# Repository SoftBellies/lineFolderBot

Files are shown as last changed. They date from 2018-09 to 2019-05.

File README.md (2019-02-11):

# Line Follower robot kit

le projet est de réaliser une soirée "initiation à l'électronique" dans le cadre d'un doctorat sauvage en numérique.

Les participants auront à construire un robot suiveur de ligne à partir d'un kit mis au point par le hackerspace.

Le présent dépot sert à la conception du kit et la rédaction de sa [notice](notice_fr.md)

# petit cahier des charges du kit

* Réalisable en moins de 4 heures en comptant le temps pour les indications, la formation des groupes, les tests.
* On initie à des techniques que les participants pourront réutiliser à la maison. Donc hormis un pistolet à colle, un fer à souder et un tourne-vis, aucun autre outil ne doit être à utiliser.
* Le robot peut être amélioré

C'est pour respecter ces trois points que je pars sur les concepts suivants:

* Le circuit électronique lors de l'atelier sera réalisé sur une plaque à pastille. Pas de création de circuits préimprimés à l'avance.
* L'utilisation d'un arduino permet de laisser une marge d'amélioration au robot (par l'ajout de capteurs ou de moteurs)

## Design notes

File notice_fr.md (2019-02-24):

# Notice de montage du robot suiveur de ligne

| Element | Quantité / notes | Image |
| :--- | :---: | ---: |
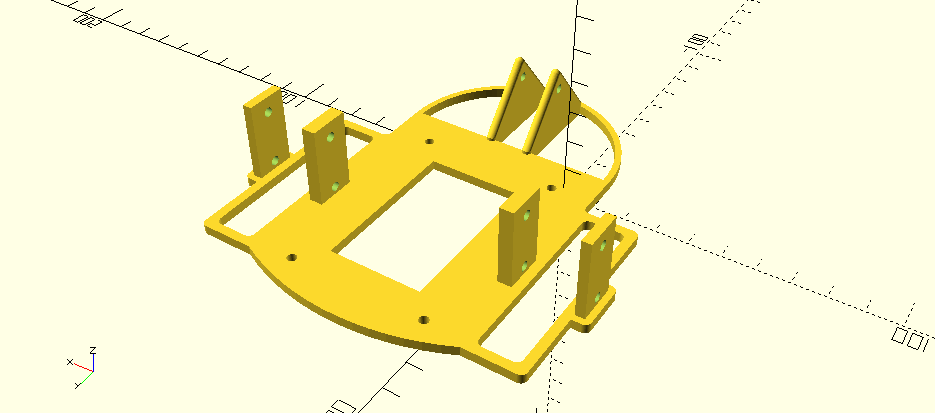
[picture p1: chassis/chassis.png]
chassis
| Chassis (impression 3D) | 1 | |
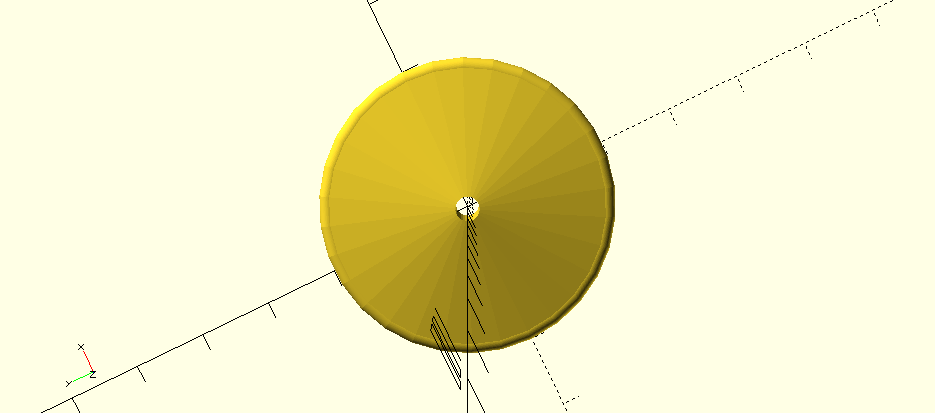
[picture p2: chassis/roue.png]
roue
|Roue arrière (impression 3D)|1||
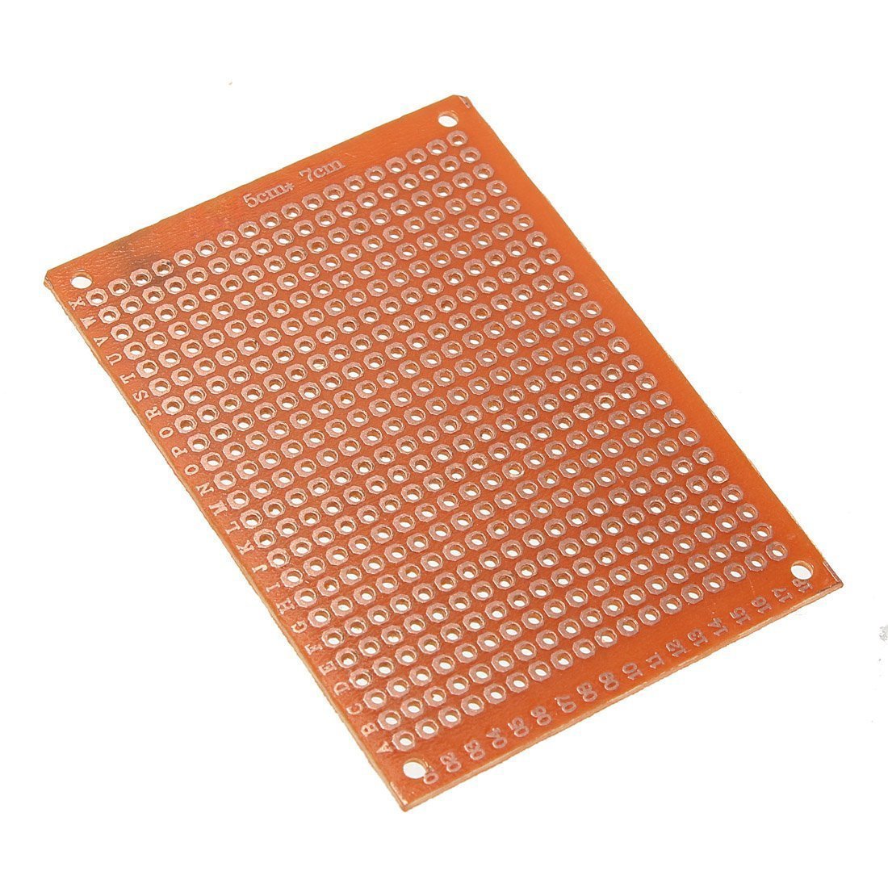
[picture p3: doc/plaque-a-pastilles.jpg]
|Plaque de prototypage à pastilles 5X7 CM|1|
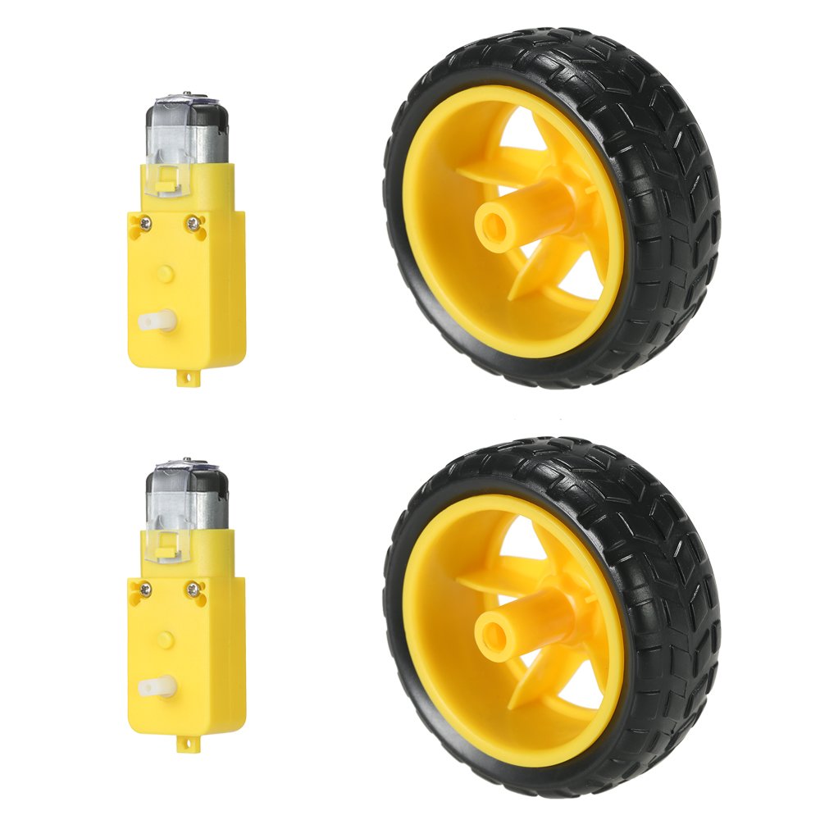
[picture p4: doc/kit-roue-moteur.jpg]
Kit roues et moteur
|kit Roues + moteur 5VDC|2|
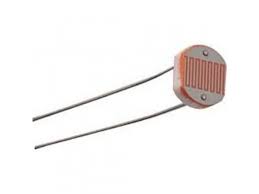
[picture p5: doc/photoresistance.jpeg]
photoresistance
|Photo résistances| 2 | |
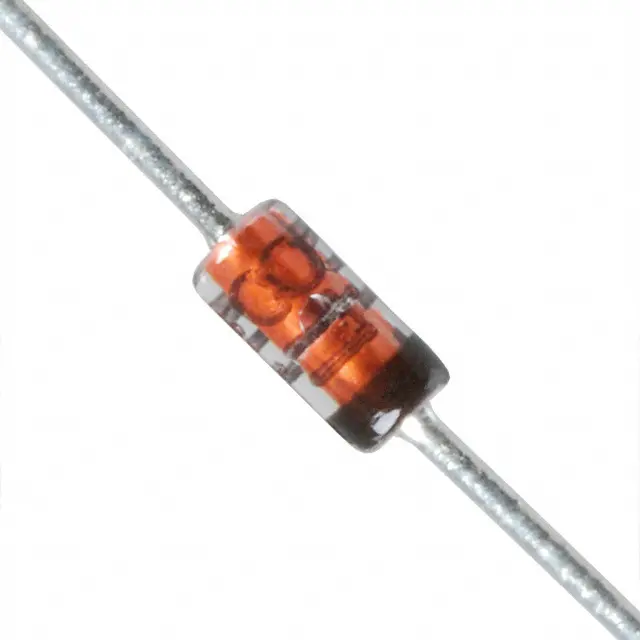
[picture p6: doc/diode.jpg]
diodes
|Diodes| 2 | |
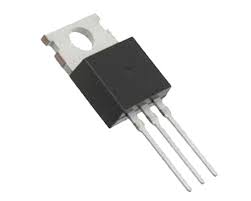
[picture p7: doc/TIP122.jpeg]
TIP122
|Transistor TIP 122| 2 | |
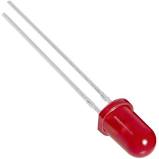
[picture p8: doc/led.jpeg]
leds
|Leds| 4 | |
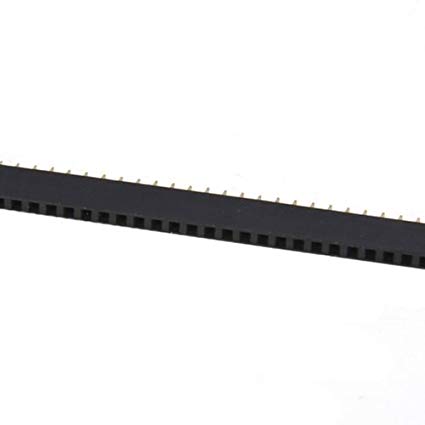
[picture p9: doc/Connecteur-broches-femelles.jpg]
connecteurs broches femelle
|Ligne connecteur broche femelle| 2x 15 + 2x2 ||

## Circuit électronique

Voici le shéma global :

Shema

La première face correspond aux pistes à créer sur la plaque à pastilles.

La seconde face est le côté composants.

### Les connecteurs femelles qui recevront l'arduino

* Prendre 2 rangées de connecteurs Pin femelles.
* Avec une pince coupante, les couper au milieu de la 16ème PIN, de façon à ce que 15 pins soient utilisables.

* Les placer sur la plaque de prototypage.

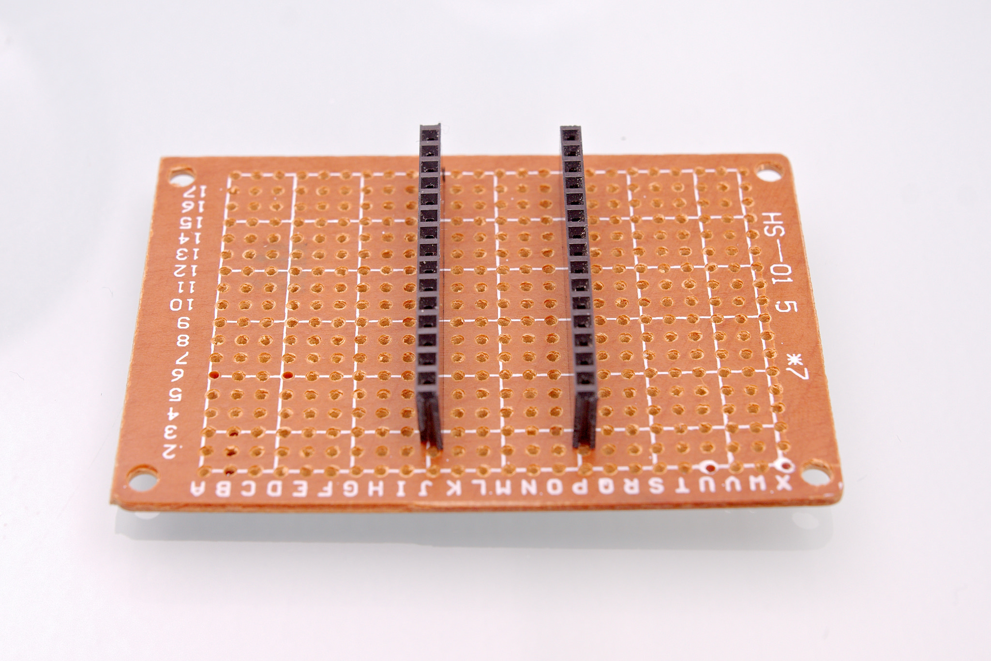
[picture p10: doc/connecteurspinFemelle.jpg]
photo connecteurs pins femelle


* Côté circuit, souder chaque pin:

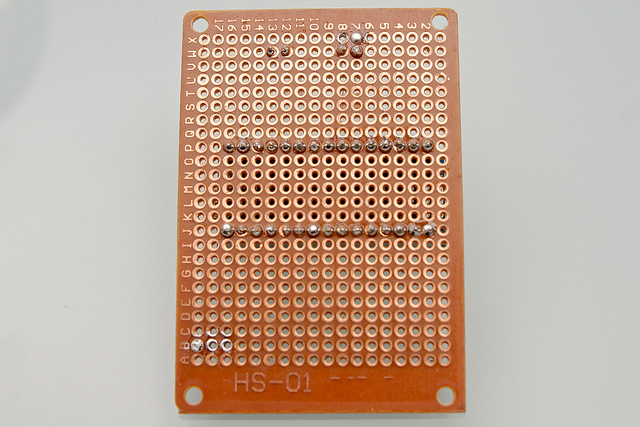
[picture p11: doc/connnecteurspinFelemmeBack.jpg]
photo connecteurs pins femelle verso


### La piste de masse

Afin de vous faire la main avec les soudures, Faites tout le circuit 5V (en rouge):

* En faisant en sorte que la continuité soit respectée.
* Sans déborder sur les pastilles d'à côté.

5V

### Souder quelques composants

* Coté composants de la plaque, placer ces trois résistances:

resistances

* Coté circuit, mettre un point de soudure sur les pattes des résistances pour les fixer (points marqués en rouge).

resistances

* Raccorder ces résistances à la masse de l'arduino:

resistances

Raccorder deux de ces résistances aux pins de l'arduino:

resistances

### Continuez !

Voila, vous avez compris, il faut placer les composants un par un, les souder et faire les lignes d'étain pour les relier conformément au circuit.

Le pas à pas s'arrête ici car c'est fastidieux à écrire. Continuez composant par composant, goutte d'étain par goutte d'étain.

Quelques subtilités cependant pour la suite:

#### Certains composants sont polarisés:

* Les LEDs; Sur le schéma, elles sont représentées vue de dessus. Le côté ayant un plat y est représenté. Disposez la LED sur votre circuit dans le même sens que sur le schéma.
* Les diodes; Un anneau noir est dessiné sur les diodes. Disposez-les en respectant le côté de l'anneau.
* Les transistors

#### le capteur doit froler le sol
Les LEDS et les photoresistances du capteur de ligne doivent être soudées de façon:
* la photoresistance doit être le plus près possible du sol
* La led ne doit pas éclairer directement la photoresistance, ses pattes doivent être plus courtes.

Comme ceci:

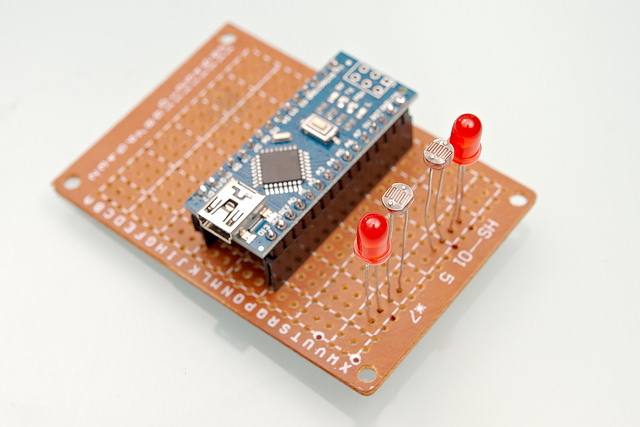
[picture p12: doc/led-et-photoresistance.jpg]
led


#### Composants sur l'autre face

Les Leds de Debugage doivent être côté circuit de la plaque, et non du même côté que les autres composants, afin qu'à la fin elles se retouvent au dessus du circuit.

## Arduino

Il faut souder les broches de l'arduino:

Le port USB doit être sur la face opposée aux broches.

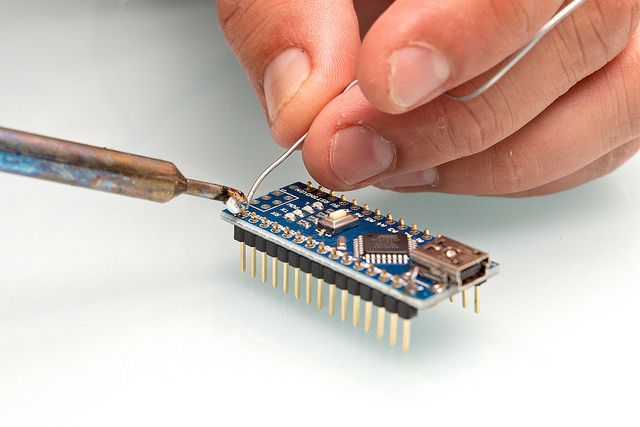
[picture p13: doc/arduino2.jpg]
arduino


## Fils  avec connecteurs Dupont sur les moteurs

Coupez un cable avec connecteurs Dupont male, dénudez-le et soudez-le sur les connecteurs du moteur. Comme ceci:

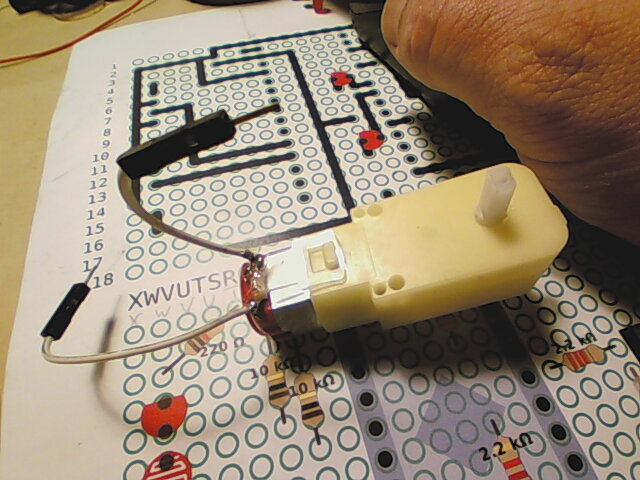
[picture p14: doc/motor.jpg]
motor


Longueur du fil, avec le connecteur: env. 7cm

## Tout assembler

Si nécessaire, contre-percez les trous dans le châssis et la plaque de prototypage.

Quelques coups de tourne-vis et vous aurez votre robot.

Il faut faire en sorte que les capteurs soient très près du sol.

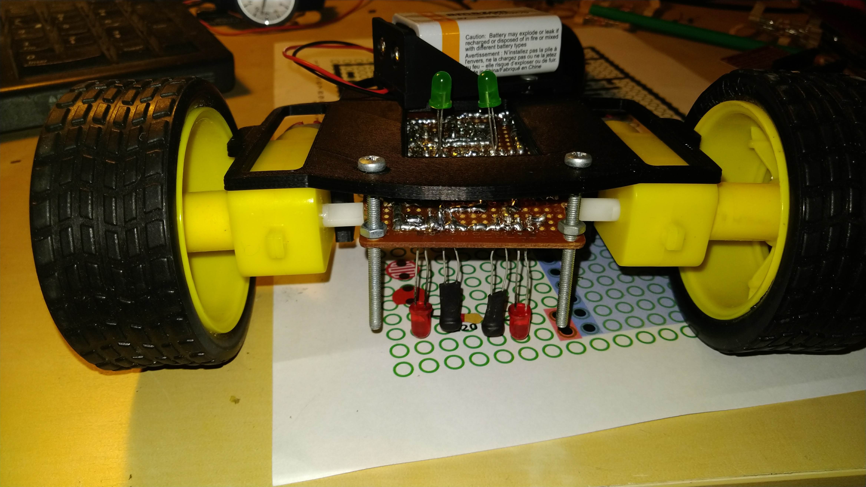
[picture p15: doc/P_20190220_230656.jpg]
robot


## Injecter le code dans l'arduino.

Il faut programmer l'arduino.

L'installation de l'environnement Arduino est expliquée sur le site officiel. https://www.arduino.cc/

Le programme servant à faire fonctionner le robot suiveur de ligne  peut être téléchargée sur la plateforme Gogs (git) du hackerspace:

https://git.ventresmous.fr/VentresMous/lineFollowerBot/src/master/lineFollowerBot/lineFollowerBot.ino

Nous vous détaillerons ces manipulations durant l'atelier.

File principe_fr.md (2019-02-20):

## Principes

### Détection de la ligne

Un sol clair reflète plus la lumière qu'un sol sombre.

En disposant de cette manière, deux LED et deux photoristances:

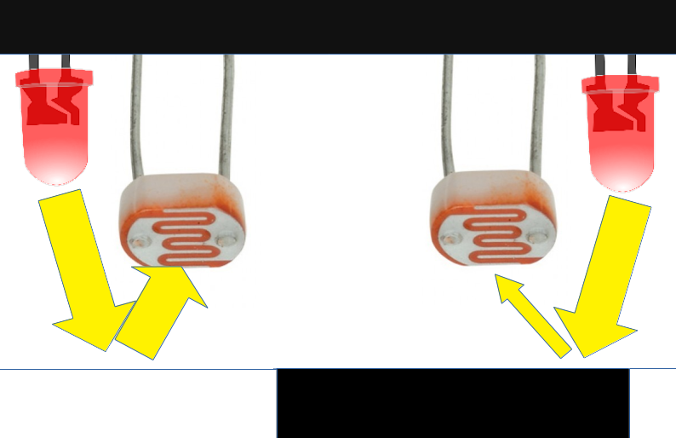
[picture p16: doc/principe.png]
schema de principe


La valeur de chaque photoresistance dépend de la quantité de lumière reflétée par le sol.

Sur le schéma ci dessus la lecture des valeurs des photorésistances permettrait de déduire que celle de droite est au dessus d'une ligne noire. Tandis que celle de gauche est au dessus d'une zone claire.

Le robot dérive donc vers la droite de la ligne. Il faut le faire tourner à gauche

### Actionner les moteurs en fonction des valeurs du capteur.

#### Présentation de l'arduino

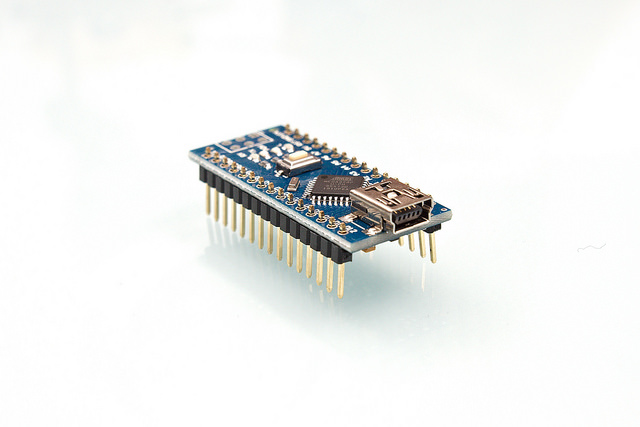
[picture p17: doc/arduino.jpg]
Arduino Nano


L'arduino est un circuit électronique programmable pouvant "lire des valeurs" via certaines pins, et déclencher des courants électriques via d'autres pins.

Grâce à cette carte pouvoir "lire" les valeurs des capteurs de luminosité, et notre programme, en fonction de ces valeurs actionnera ou non l'envoi d'une tension électrique dans les moteurs.

#### Lecture d'une valeur

#### déclenchement d'un moteur

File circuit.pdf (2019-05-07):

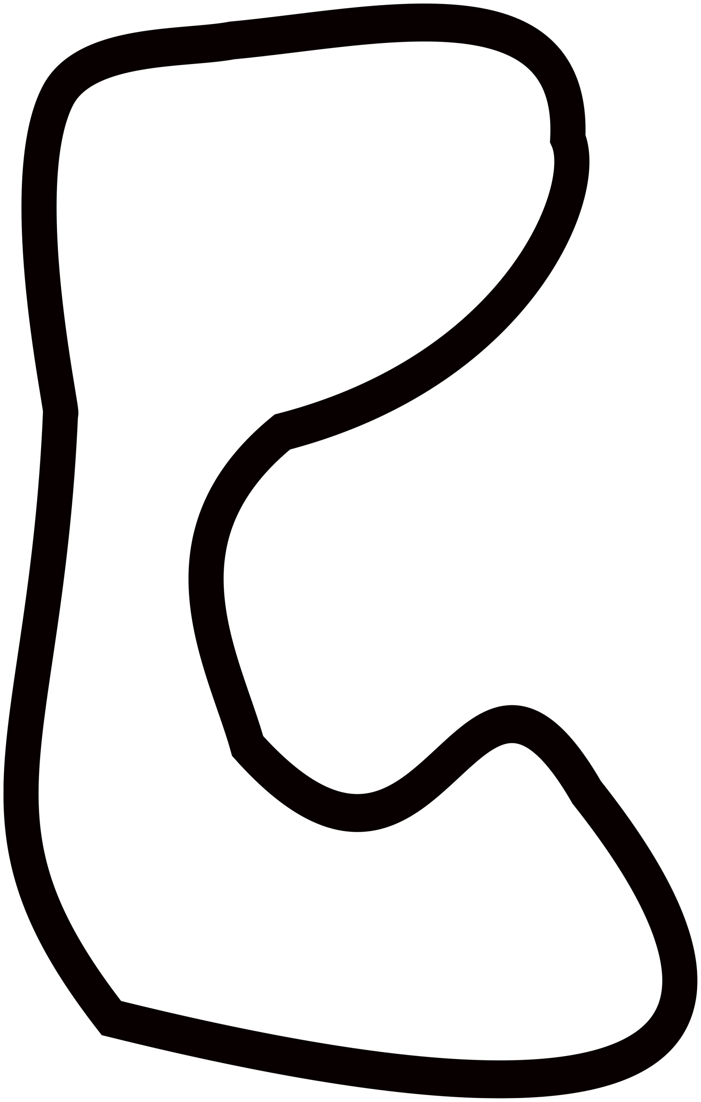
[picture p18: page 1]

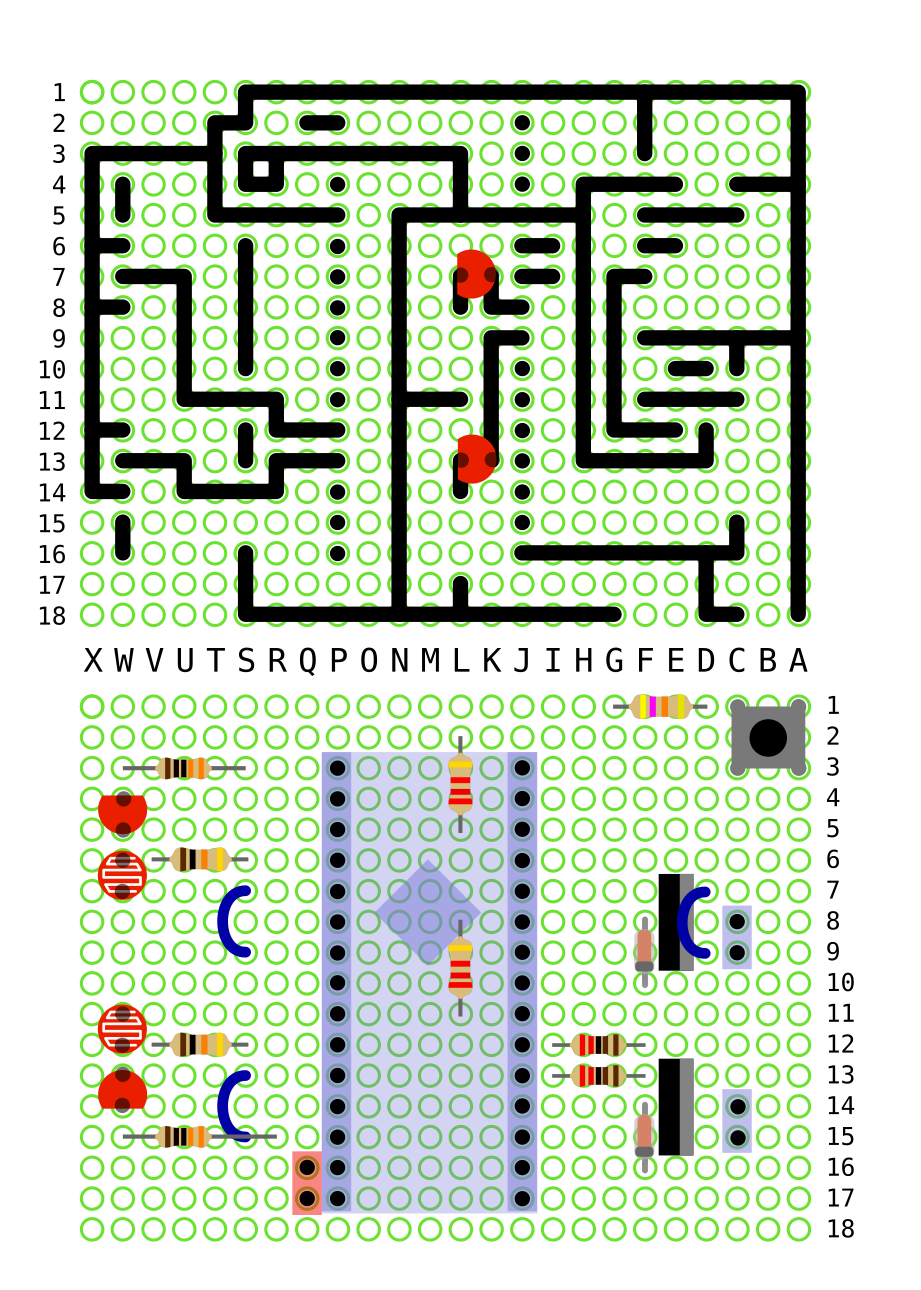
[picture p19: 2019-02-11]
electronics/robot-soudure-composants.png

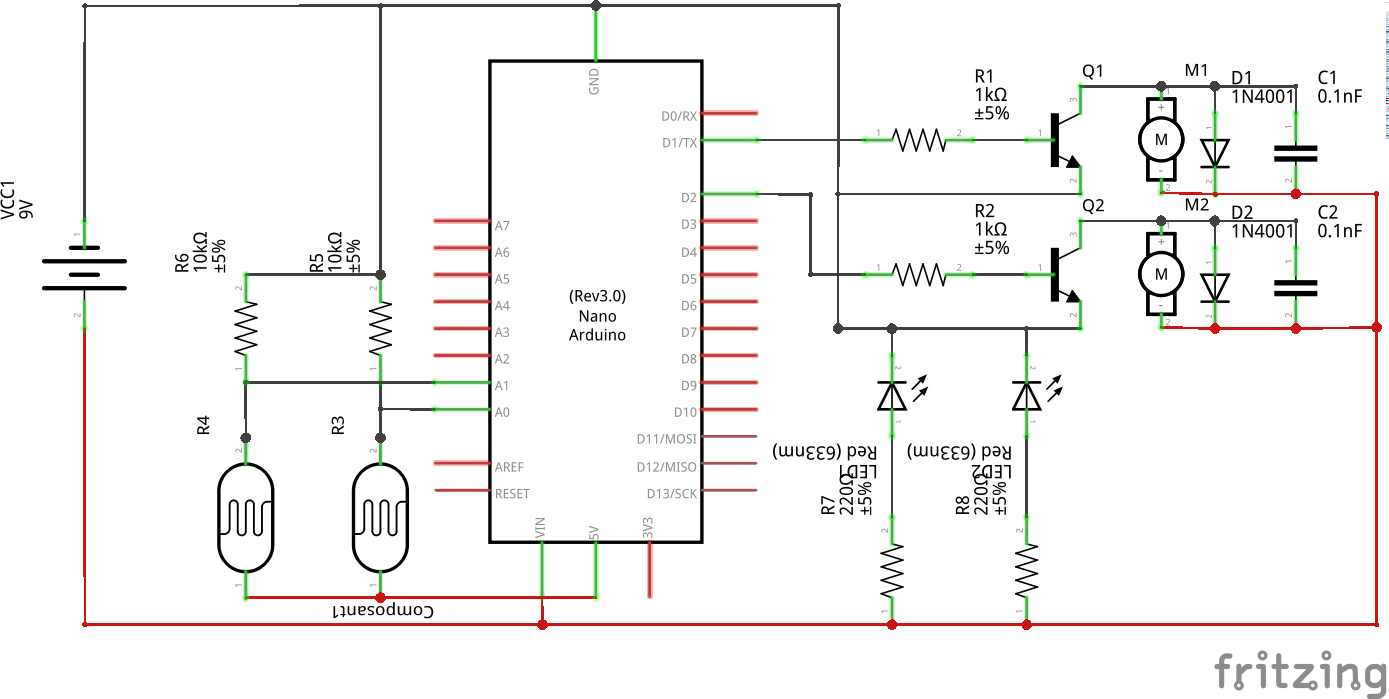
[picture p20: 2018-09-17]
electronics/robot-plus simple_schema.png

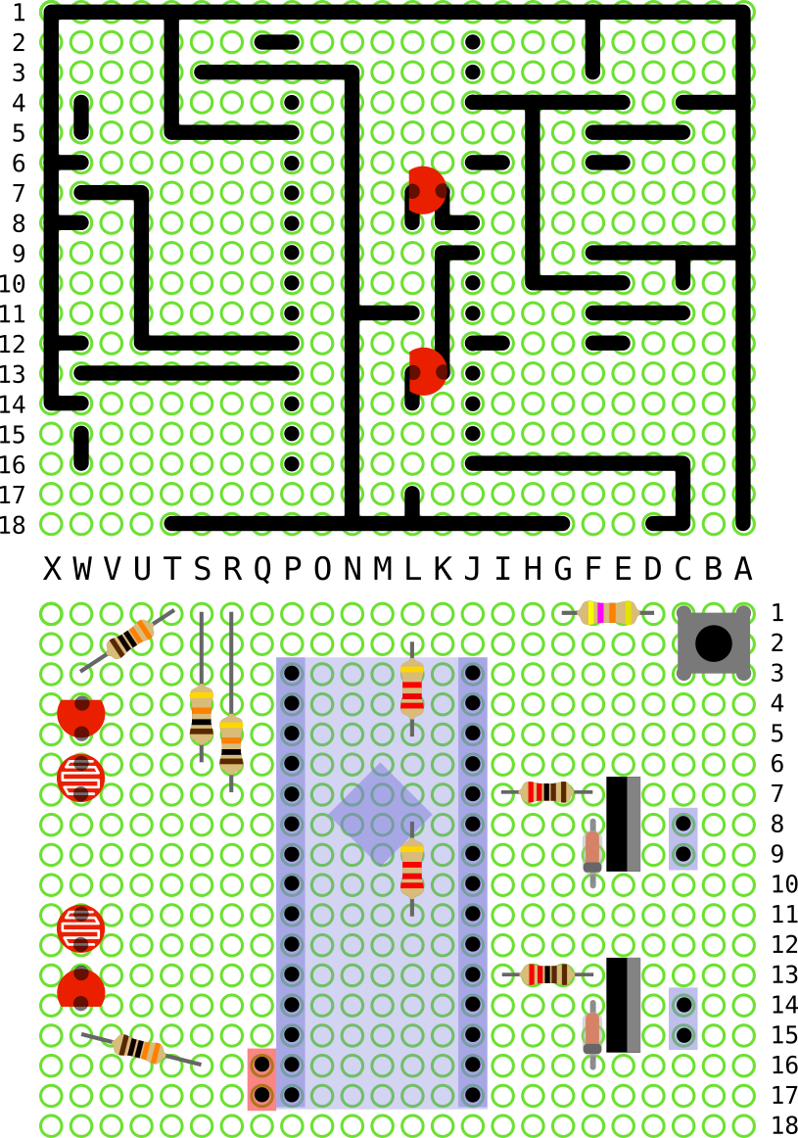
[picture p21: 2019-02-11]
electronics/robot-soudure-composants-v2.png

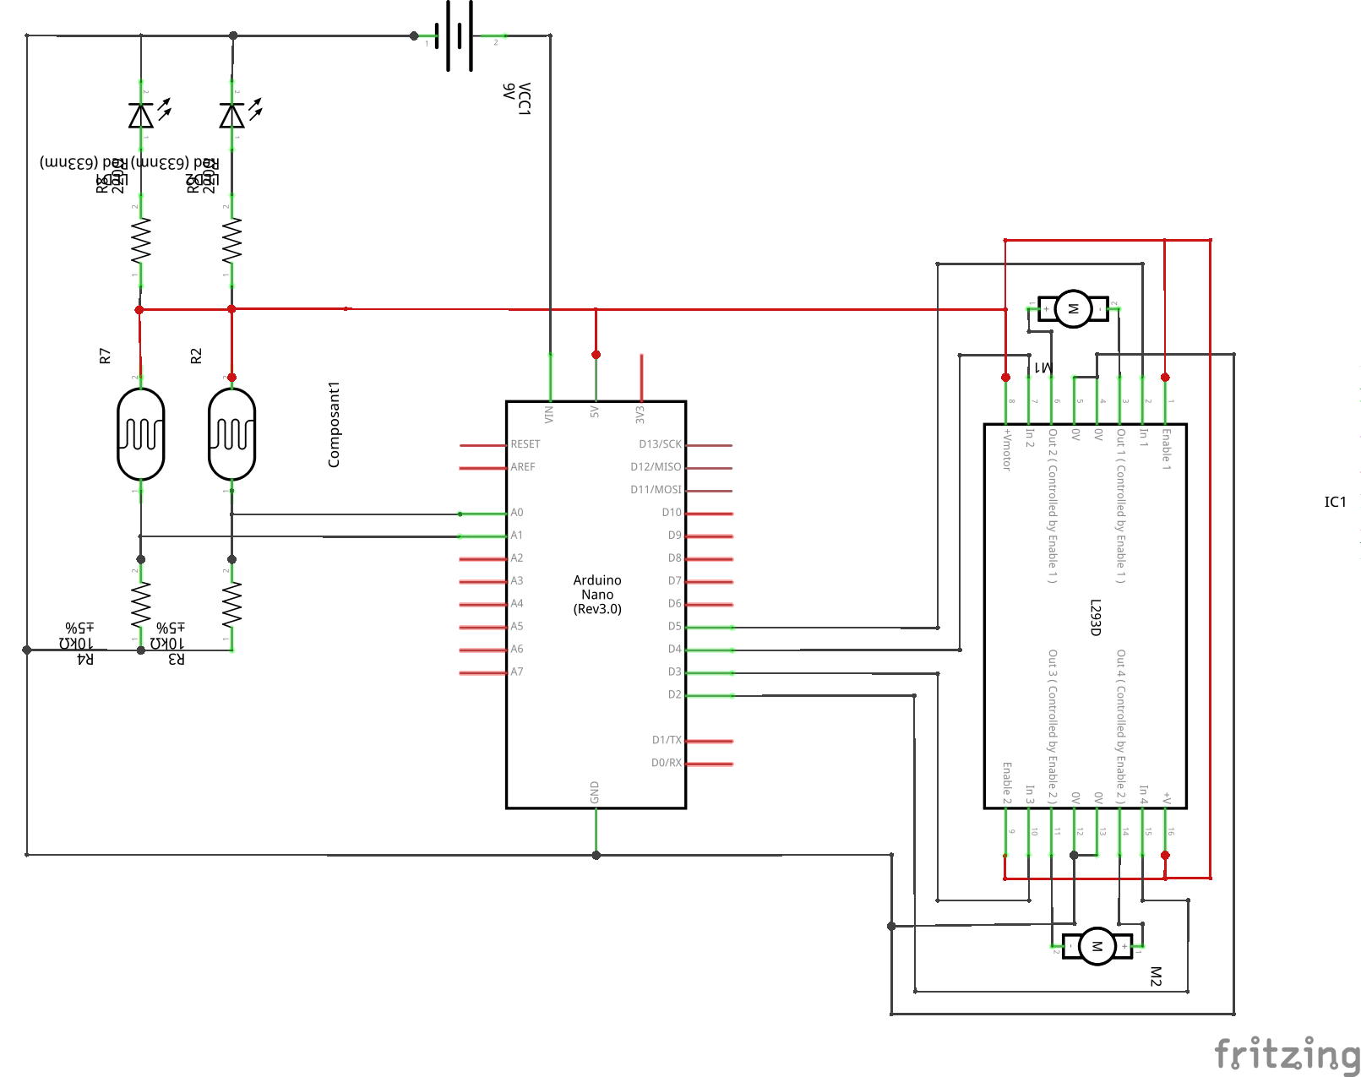
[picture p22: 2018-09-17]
electronics/robot-avec-l293d_schema.png

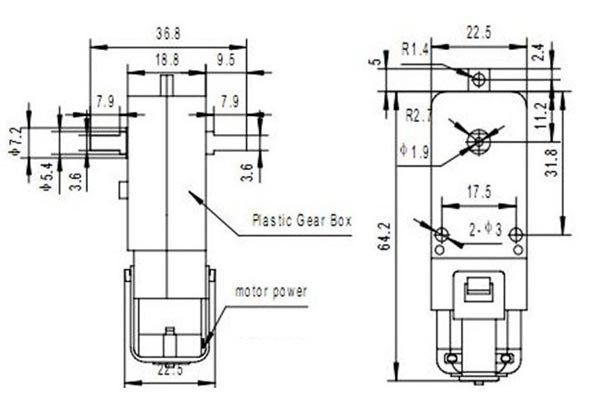
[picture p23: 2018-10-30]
chassis/SKU116853 (3).JPG

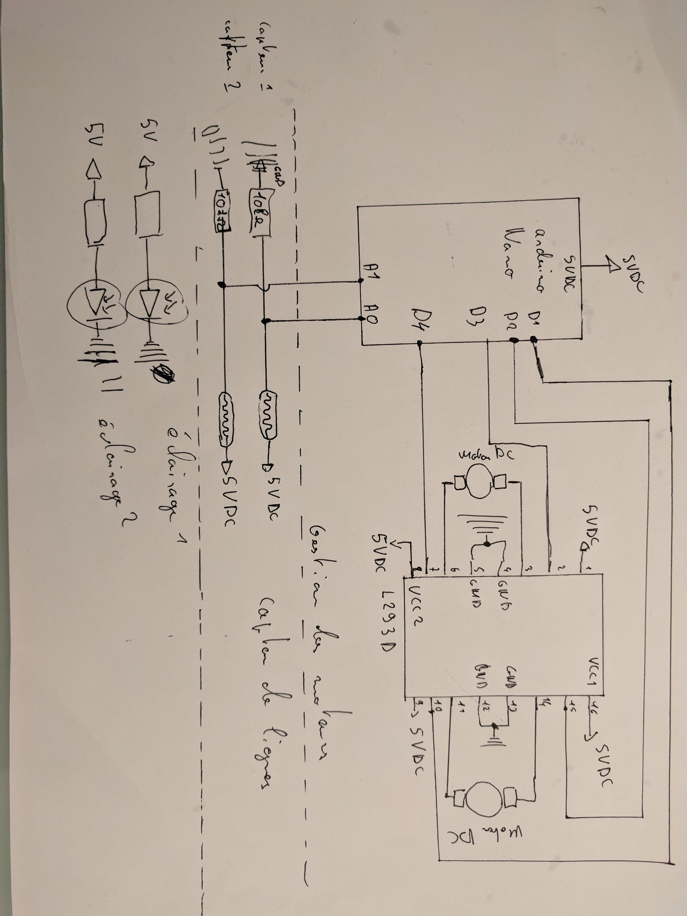
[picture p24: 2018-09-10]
scheme.jpg

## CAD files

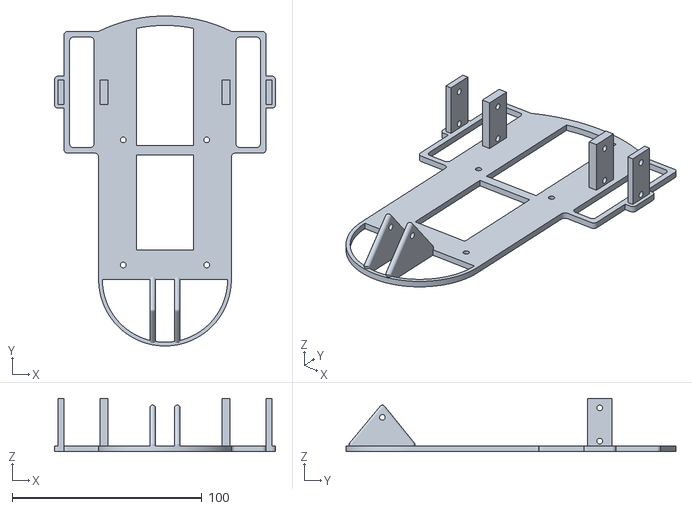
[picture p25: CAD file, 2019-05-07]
chassis/chassis2.stl
116.6 x 174.0 x 28.0

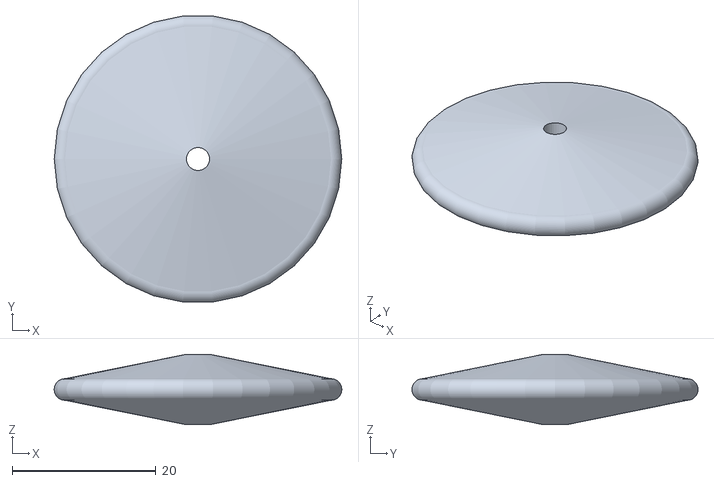
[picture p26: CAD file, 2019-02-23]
chassis/roue.stl
40.0 x 39.8 x 9.80

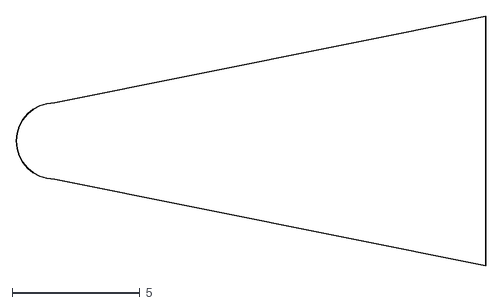
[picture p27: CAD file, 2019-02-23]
chassis/profil-roue.dxf
18.4 x 9.80

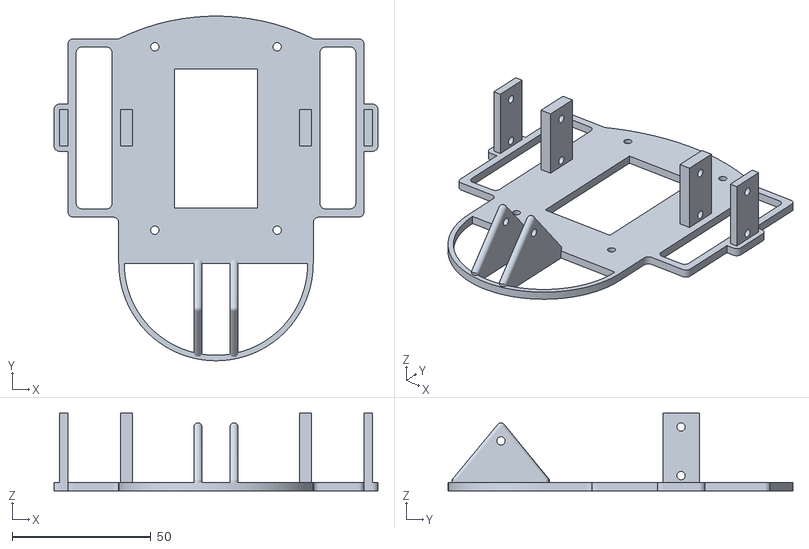
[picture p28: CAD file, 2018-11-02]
chassis/chassis.stl
116.6 x 124.0 x 28.0

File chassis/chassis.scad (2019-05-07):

difference(){
    
    union(){    
        linear_extrude (height=3)
            import (file="chassis.dxf", layer="chassis", $fn=100);
        
        
        //pates de fixation des moteurs
        translate ([0,0,2.99])
            linear_extrude (height=25)
            import (file="chassis.dxf", layer="chassis-fixation-moteur", $fn=100);
      
        
    
       
  //fixation 3ème roue
  hull(){    
      
              translate ([0,0,2.99])
            linear_extrude (height=1)
            import (file="chassis.dxf", layer="3emeRoueG", $fn=100);
        
        translate ([18.5,-75.8,23])
            sphere(r=1.5, $fn=50);
        }
        
         hull(){    
            translate ([0,0,2.99])
            linear_extrude (height=1)
            import (file="chassis.dxf", layer="3emeRoueD", $fn=100);
        translate ([31.5,-75.8,23])
            sphere(r=1.5, $fn=50);
        }
    }
    
   
   union(){
       
       //trous pour les vis
       translate([-50,38.8,5.5])
       rotate([0,90,0])
        #cylinder(h = 150, r1 = 1.5, r2 = 1.5, center = true/false, $fn=100);
       
       translate([-50,38.8, 23])
       rotate([0,90,0])
        #cylinder(h = 150, r1 = 1.5, r2 = 1.5, center = true/false, $fn=100);
     
      
       //14.25
              translate([-50,-75.8, 18])
       rotate([0,90,0])
        #cylinder(h = 150, r1 = 1.5, r2 = 1.5, center = true/false, $fn=100);
   }
   
}
   

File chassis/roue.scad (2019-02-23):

   rotate_extrude (height=25)
            import (file="profil-roue.dxf", layer="0", $fn=100);
           

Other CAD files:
chassis/chassis.dxf

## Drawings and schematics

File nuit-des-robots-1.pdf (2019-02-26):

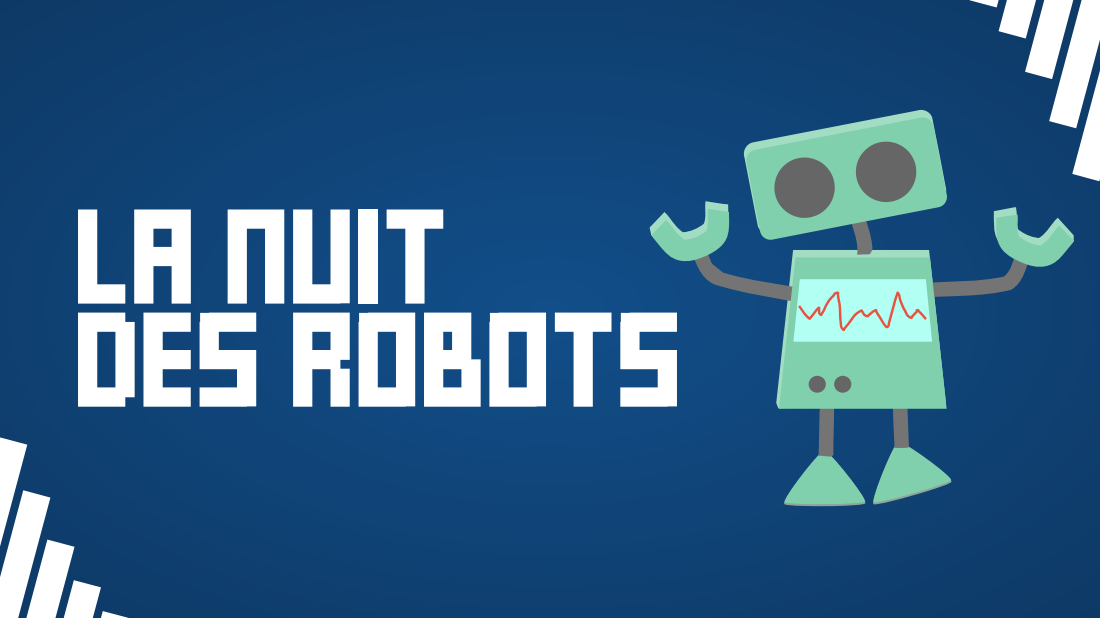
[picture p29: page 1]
LA NUIT DES ROBOTS

# robot \ʁɔ.bo\

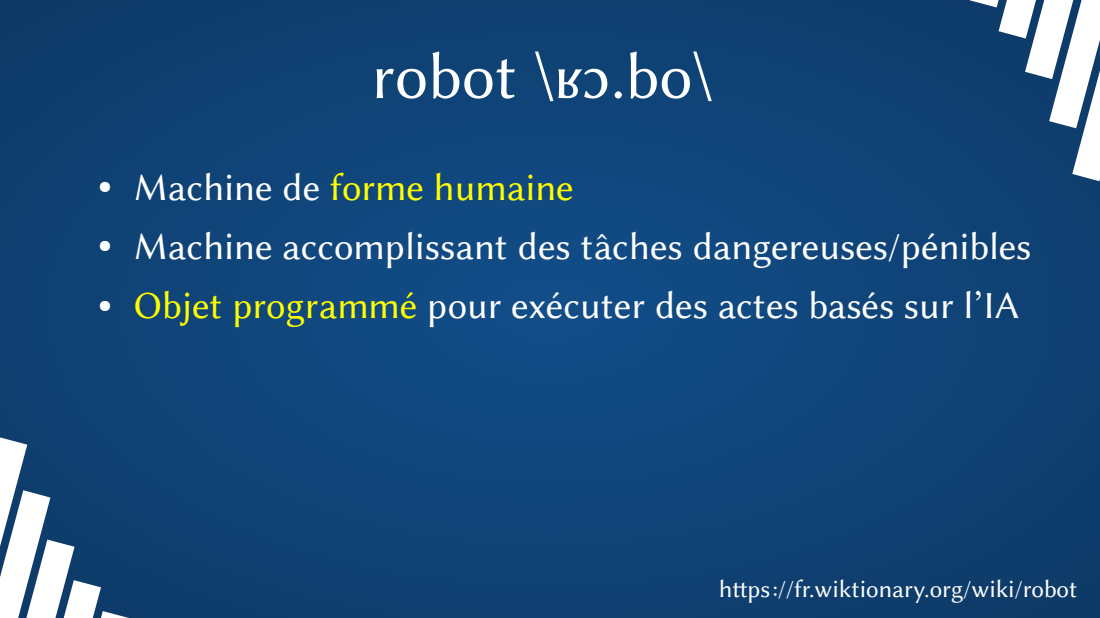
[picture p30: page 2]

● Machine de forme humaine
● Machine accomplissant des tâches dangereuses/pénibles
● Objet programmé pour exécuter des actes basés sur l’IA

htps://fr.wiktionary.org/wiki/robot

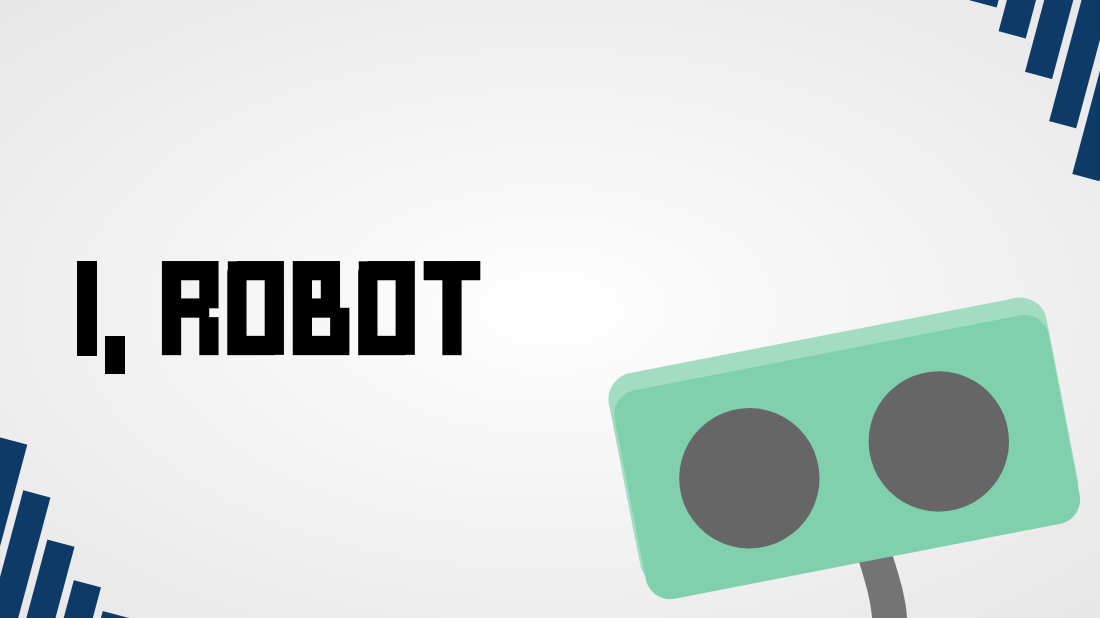
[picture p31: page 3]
I, ROBOT

# Un robot

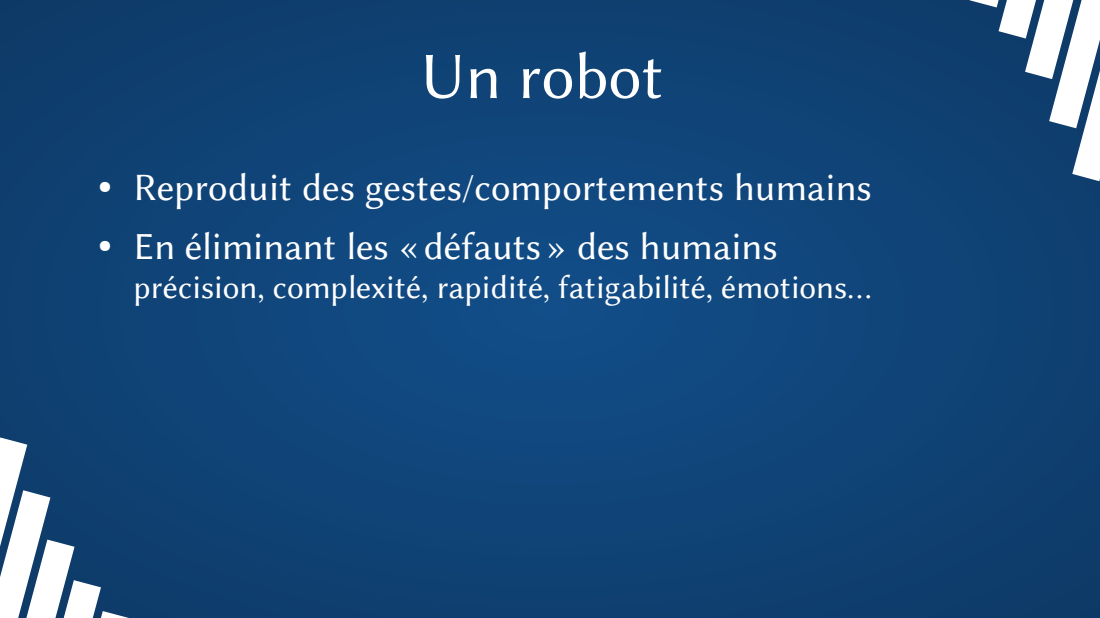
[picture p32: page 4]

● Reproduit des gestes/comportements humains
● En éliminant les «défauts» des humains
précision, complexité, rapidité, fatigabilité, émotions…

# Humain simplifié

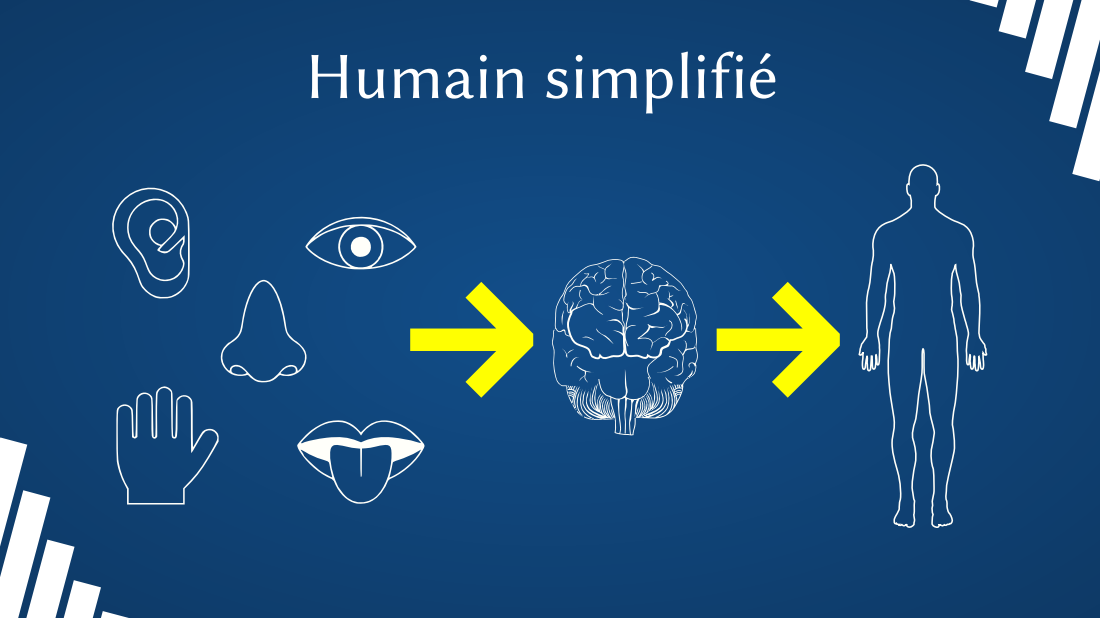
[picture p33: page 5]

# Notre robot

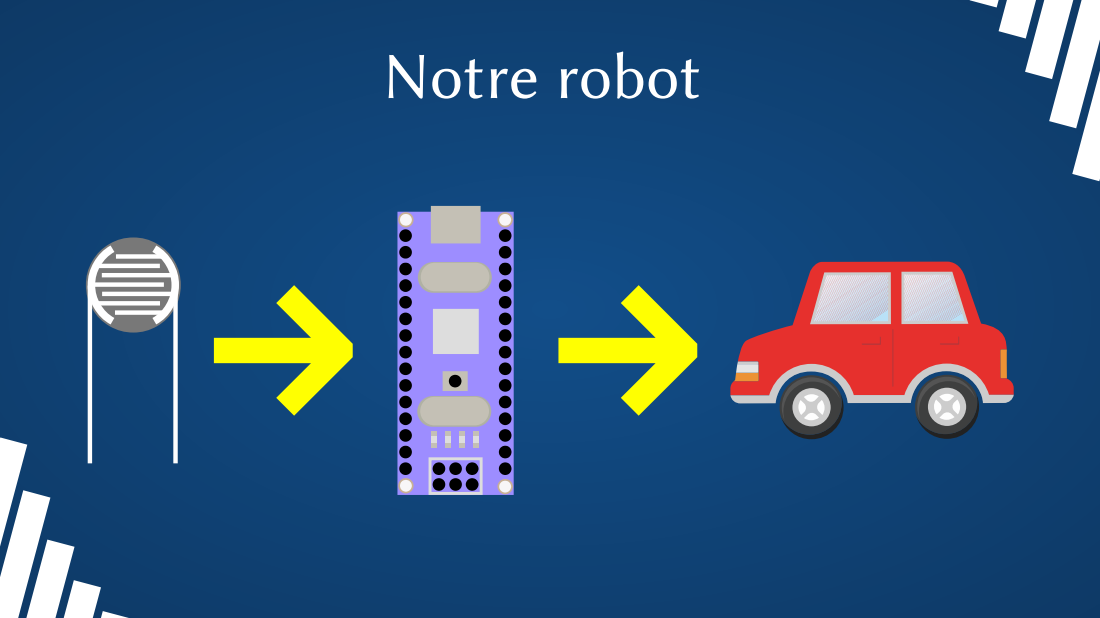
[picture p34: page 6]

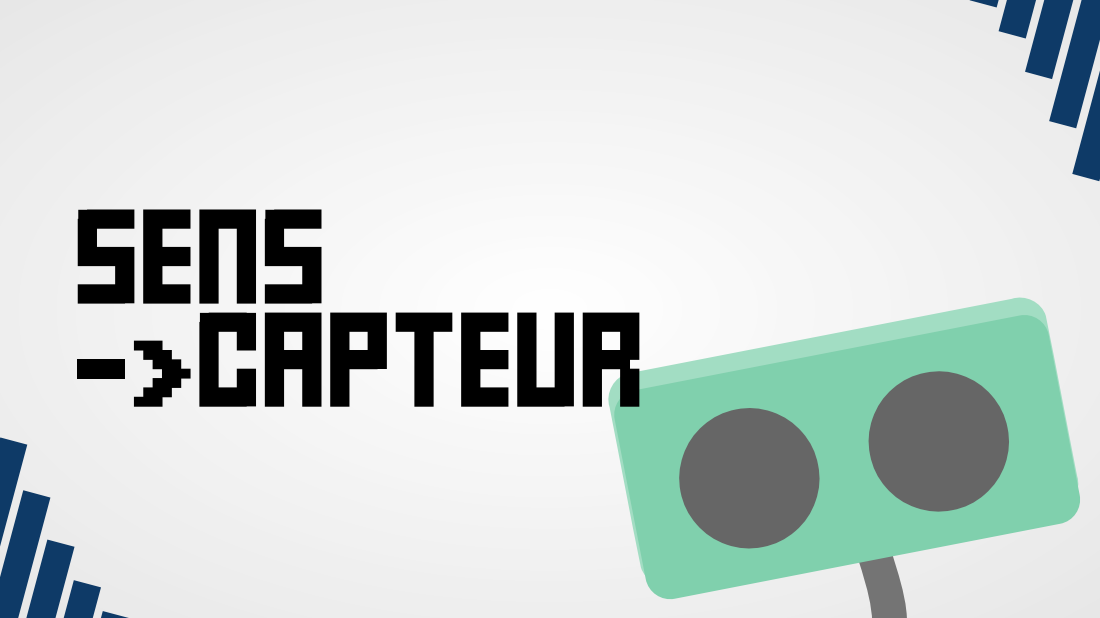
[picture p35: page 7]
SENS ->CAPTEUR

# Photo-résistance

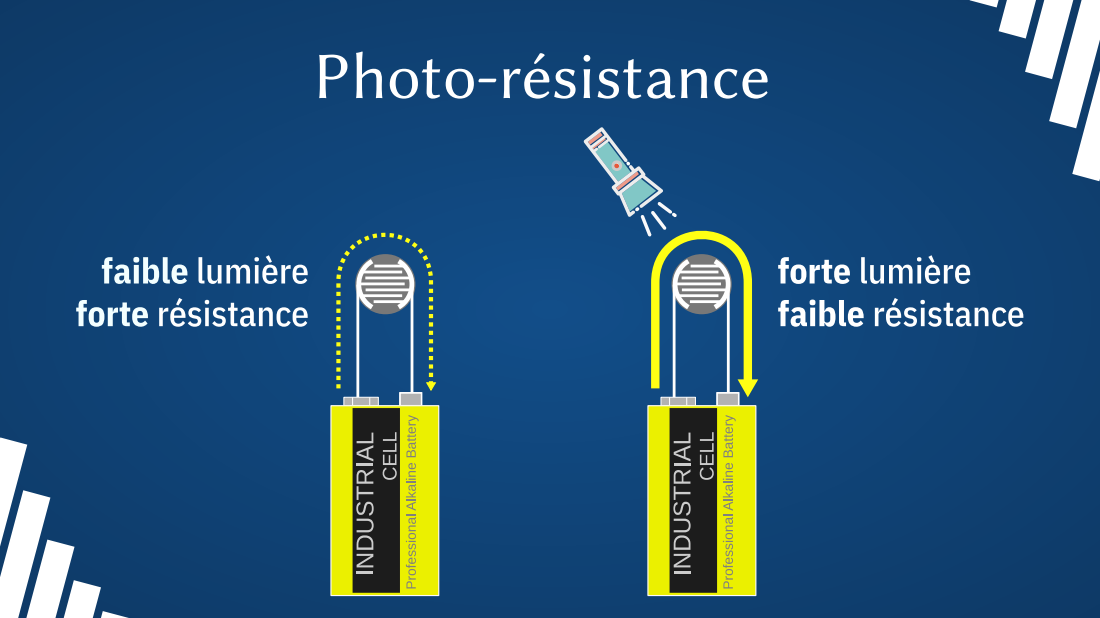
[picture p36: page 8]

# Lecture d’une photo-résistance

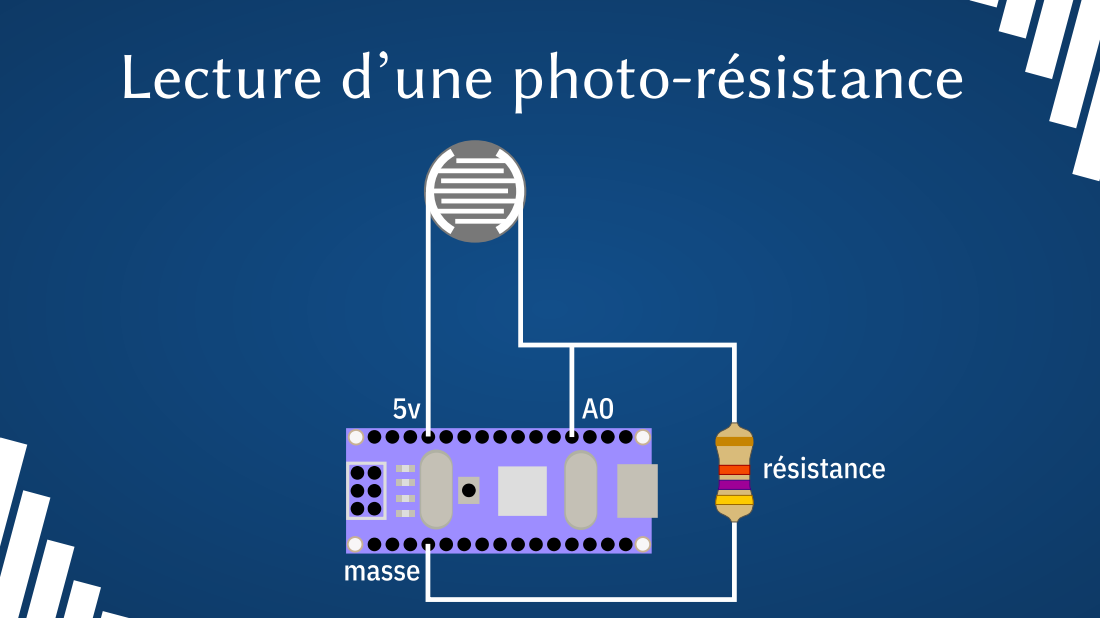
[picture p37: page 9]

# Optimisation/simplification

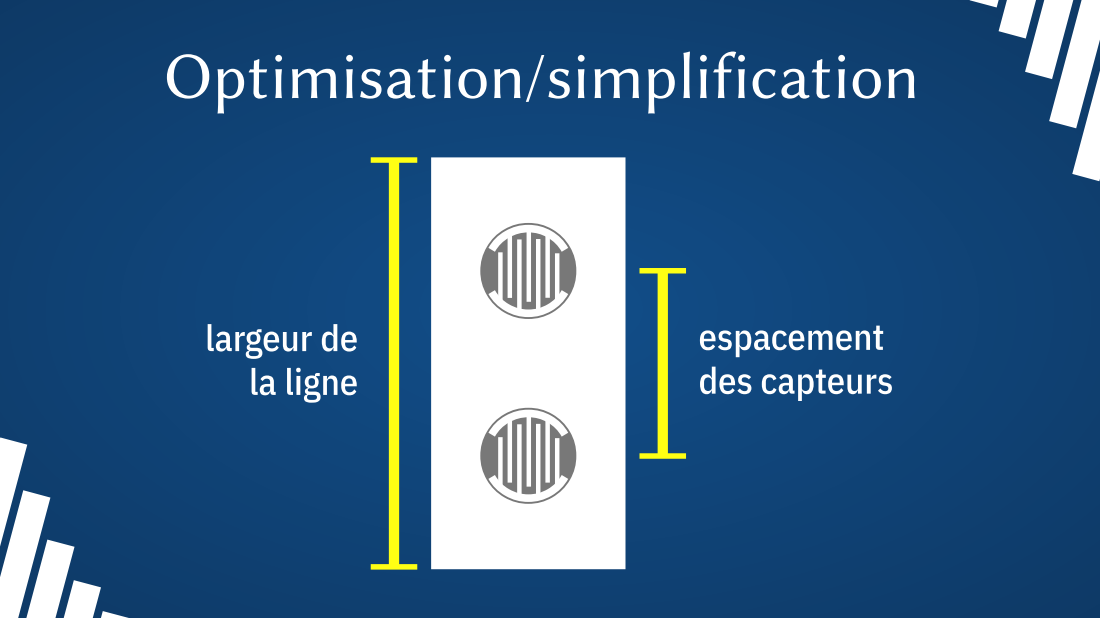
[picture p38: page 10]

# Suivre la ligne

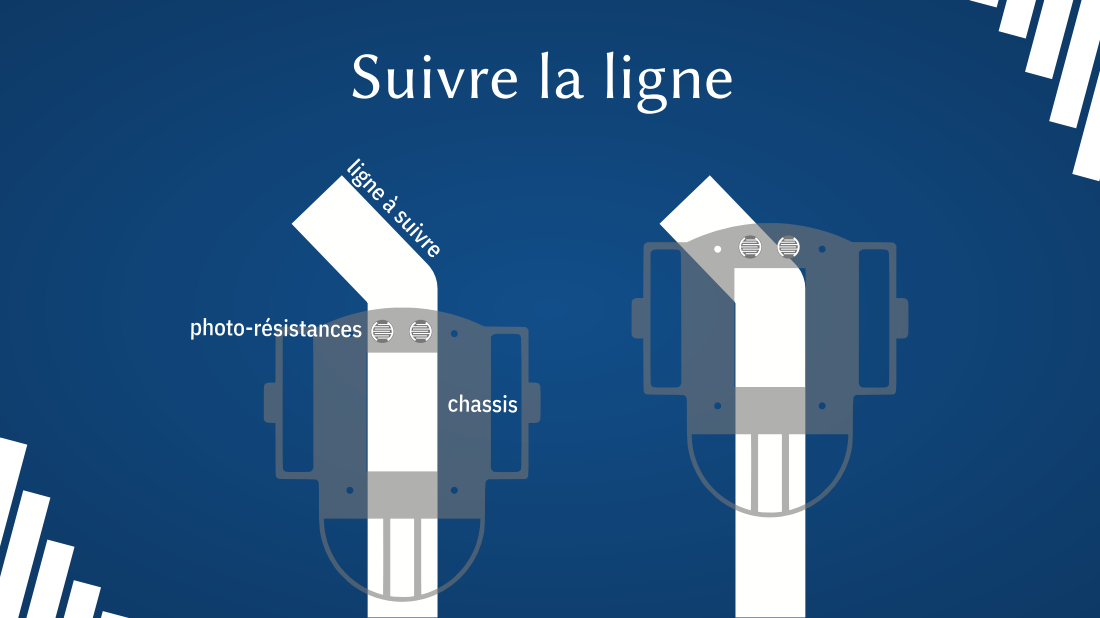
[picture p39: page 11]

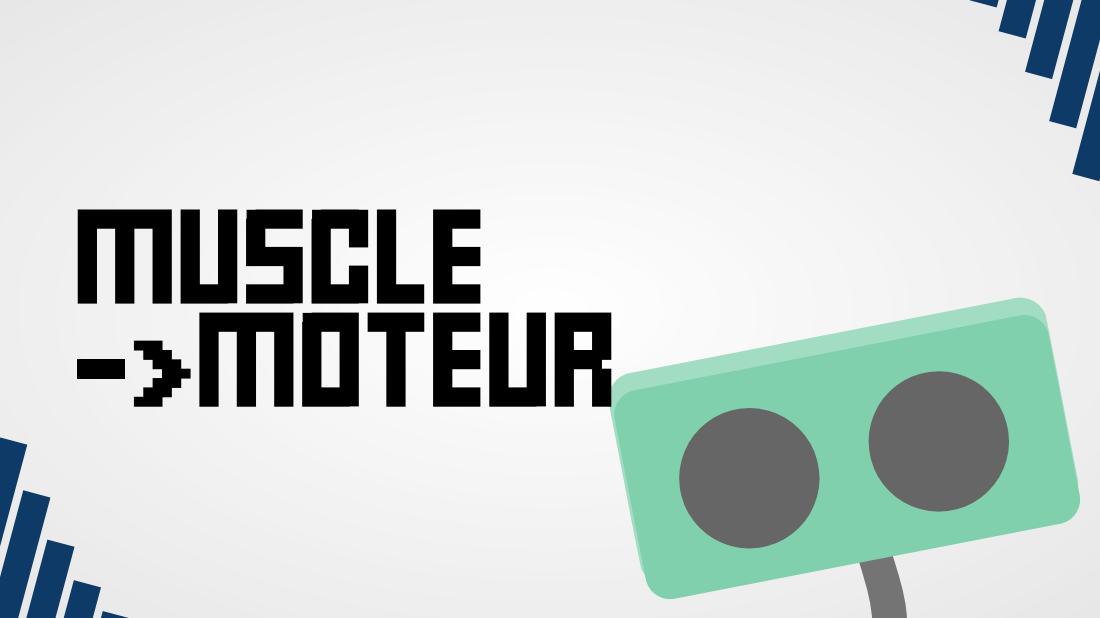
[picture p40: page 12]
MUSCLE ->MOTEUR

# À savoir


● Un Arduino ne peut pas alimenter un moteur
● Les moteurs électriques induisent du courant
si celui-ci est négatif, il est néfaste pour l’électronique
● Il est alors nécessaire d’utiliser un transistor et une diode
● Notre robot ne sait pas reculer

# Contrôle d’un moteur


COMPORTEMENT ->PROGRAMME

# 4 situations possibles


# 4 situations possibles



A VOUS DE JOUER!

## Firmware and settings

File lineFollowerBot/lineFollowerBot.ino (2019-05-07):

// lineFollowerBot.ino
// Programme basique permettant à un robot de suivre une ligne dessinée au sol.
//
// Un projet du hackerspace Ventres Mous.

// =============================================================================
//
// IDENTIFICATION DES BROCHES DE L’ARDUINO UTILISÉES PAR LE PROJET
//
// =============================================================================

// Chaque broche de l’Arduino est identifiée par un numéro. Afin de faciliter
// la lecture du code, on leur donne des noms parlants.

// Broches sur lesquelles les moteurs sont connectés.
// Ce sont des broches de sortie numériques.
#define MOTEUR_GAUCHE 2
#define MOTEUR_DROITE 8

// Broches sur lesquelles les capteurs sont connectés.
// Ce sont des broches de lecture analogique.
#define CAPTEUR_GAUCHE A0
#define CAPTEUR_DROITE A1

// Broches sur lesquelles les leds de suivi d’étalonnage sont connectées.
// Ce sont des broches de sortie numériques.
#define ETALONNAGE_LED_GAUCHE 4
#define ETALONNAGE_LED_DROITE 5

// Broche sur laquelle le bouton d’étalonnage est connecté.
// C’est une broche de lecture numérique.
#define ETALONNAGE_BOUTON 12

// Les 2 états possible du bouton d’étalonnage : pressé et relevé.
#define BOUTON_PRESSE 1
#define BOUTON_RELEVE 0


// Variables utilisées pour définir les seuils de détection des capteurs. Les
// seuils sont réglés à 200 par défaut.
int seuil_gauche = 200;
int seuil_droite = 200;

// =============================================================================
//
// INITIALISATION DES BROCHES DE L’ARDUINO
//
// =============================================================================

// Cette fonction est exécutée une seule fois lors de l’allumage de l’Arduino.
// Son rôle consiste à configurer l’Arduino pour un usage précis, dans le cas
// présent pour un robot suiveur de ligne.
void setup() {
  // Configure les broches des moteurs en sortie numérique. Ces broches seront
  // soit à 0 volt, soit à 5 volts. Les broches de l’Arduino ne sont pas faites
  // pour alimenter un moteur, elles serviront à piloter des transistors qui,
  // eux, alimenteront les moteurs.
  pinMode(MOTEUR_GAUCHE, OUTPUT);
  pinMode(MOTEUR_DROITE, OUTPUT);

  // Configure les broches des leds de suivi d’étalonnage en sortie numérique.
  // Les leds consomment très peu d’énergie, elles seront directement pilotées
  // par les broches de l’Arduino.
  pinMode(ETALONNAGE_LED_GAUCHE, OUTPUT);
  pinMode(ETALONNAGE_LED_DROITE, OUTPUT);

  // Configure la broche du bouton d’étalonnage en entrée numérique.
  pinMode(ETALONNAGE_BOUTON, INPUT);

  // Les broches analogiques des capteurs sont obligatoirement en mode lecture
  // analogique. Il n’y a donc pas de réglage à faire sur ces broches.
  Serial.begin(9600);
}

// =============================================================================
//
// GESTION DU BOUTON D’ÉTALONNAGE
//
// =============================================================================

// Attend jusqu’à ce que le bouton d’étalonnage soit enfoncé ou relaché.
// Le paramètre etat peut prendre 2 valeurs : BOUTON_PRESSE et BOUTON_RELEVE.
// Si la fonction est appelée avec BOUTON_PRESSE, elle ne laissera le programme
// continuer que si le bouton est enfoncé. Si elle est appelée avec
// BOUTON_RELEVE, elle ne laissera le programme continuer que si le bouton est
// relevé.
void continuer_si(int etat) {
  while(digitalRead(ETALONNAGE_BOUTON) != etat) delay(1);
}

// =============================================================================
//
// GESTION DES LEDS D’ÉTALONNAGE
//
// =============================================================================

// Fait clignoter les leds d’étalonnage pour indiquer à l’utilisateur que
// l’étalonnage est terminé.
void clignoter() {
  // Fait clignoter 5 fois les leds. Clignoter consiste à allumer puis éteindre.
  for(int b = 0; b < 5; b++) {
    // Allume les leds d’étalonnage (les broches sont réglées à 5 volts).
    digitalWrite(ETALONNAGE_LED_GAUCHE, HIGH);
    digitalWrite(ETALONNAGE_LED_DROITE, HIGH);

    // Attend 0,2 secondes (200 millisecondes).
    delay(200);

    // Éteint les leds d’étalonnage (les broches sont réglées à 0 volt).
    digitalWrite(ETALONNAGE_LED_GAUCHE, LOW);
    digitalWrite(ETALONNAGE_LED_DROITE, LOW);

    // Attend 0,2 secondes (200 millisecondes).
    delay(200);
  }
}

// Éteint les deux leds d’étalonnage.
void eteindre() {
  // Éteint les 2 leds de débogage en mettant leurs broches à 0 volt.
  digitalWrite(ETALONNAGE_LED_GAUCHE, LOW);
  digitalWrite(ETALONNAGE_LED_DROITE, LOW);
}

// =============================================================================
//
// ÉTALONNAGE DES CAPTEURS DU ROBOT
//
// =============================================================================

// Étalonne les capteurs pour établir la différence entre la ligne et le sol.
void etalonnage() {
  // Variables qui vont recevoir les valeurs minimales et maximales des capteurs
  // gauche et droite (L’unité importe peu). Elles permettent de garder en
  // mémoire l’état du capteur afin de pouvoir effectuer des calculs plus tard.
  int min_gauche;
  int min_droite;
  int max_gauche;
  int max_droite;

  // Arrête les 2 moteurs, le robot ne bouge plus.
  moteur_arret();

  // L’étalonnage est déclenché quand l’utilisateur appuie sur le bouton
  // d’étalonnage. On attend que le bouton soit relaché pour étalonner.
  continuer_si(BOUTON_RELEVE);
  Serial.println("BOUTON_RELEVE");

  // Lit l’état des deux capteurs.
  min_gauche = analogRead(CAPTEUR_GAUCHE);
  min_droite = analogRead(CAPTEUR_DROITE);

  // Éteint les deux leds d’étalonnage.
  eteindre();

  // Attend que l’utilisateur clique sur le bouton (clic = appui + relache).
  continuer_si(BOUTON_PRESSE);
  continuer_si(BOUTON_RELEVE);
  Serial.println("BOUTON_PRESSE_RELEVE");

  // Lit l’état des deux capteurs.
  max_gauche = analogRead(CAPTEUR_GAUCHE);
  max_droite = analogRead(CAPTEUR_DROITE);

  // Le seuil correspond à la valeur située entre les valeurs minimales et
  // maximales que le capteur retourne.
  seuil_gauche = (min_gauche + max_gauche) / 2;
  seuil_droite = (min_droite + max_droite) / 2;
  Serial.println("FIN_ETALONNAGE");

  clignoter();
}

// =============================================================================
//
// GESTION DES DEUX MOTEURS
//
// =============================================================================

// Arrête les deux moteurs. Le robot ne bouge plus.
void moteur_arret() {
  Serial.println("ARRET_MOTEUR");
  digitalWrite(MOTEUR_GAUCHE, LOW);
  digitalWrite(MOTEUR_DROITE, LOW);
}

// Fait tourner le robot à droite.
void moteur_droite() {
  // Pour tourner à droite, on bloque le côté droit et on fait avancer le côté
  // gauche.
  Serial.println("MOTEUR_DROITE");

  digitalWrite(MOTEUR_GAUCHE,HIGH);
  digitalWrite(MOTEUR_DROITE,LOW);
}

// Fait tourner le robot à gauche.
void moteur_gauche() {
  // Pour tourner à gauche, on bloque le côté gauche et on fait avancer le côté
  // droit.
  Serial.println("MOTEUR_GAUCHE");
  digitalWrite(MOTEUR_GAUCHE, LOW);
  digitalWrite(MOTEUR_DROITE, HIGH);
}

// Fait tourner les deux moteurs. Le robot avance.
void moteur_avance() {
  Serial.println("MOTEUR_AVANCE");
  digitalWrite(MOTEUR_GAUCHE, HIGH);
  digitalWrite(MOTEUR_DROITE, HIGH);
}

// =============================================================================
//
// BOUCLE PRINCIPALE
//
// =============================================================================

// La fonction loop est appelée en boucle par l’Arduino. Un Arduino est prévu
// pour ce genre de tâche : exclusive et répétitive.
// Le programme considère que le robot démarre la ligne entre les deux capteurs.
void loop() {
  // Variables qui vont recevoir les valeurs des capteurs.
  int valeur_gauche;
  int valeur_droite;

  // Si le bouton d’étalonnage est pressé, on lance l’étalonnage.
  if(digitalRead(ETALONNAGE_BOUTON) == 1){ 
    etalonnage();
  }

  // Lit l’état des deux capteurs.
  valeur_gauche = analogRead(CAPTEUR_GAUCHE);
  valeur_droite = analogRead(CAPTEUR_DROITE);

  // Fait avancer le robot si les deux capteurs identifient le sol.
  if((valeur_gauche < seuil_gauche) && (valeur_droite < seuil_droite)) {
    moteur_avance();
    return;
  }

  // Tourne à droite si le capteur de gauche identifie le sol et le capteur de
  // droite identifie la ligne. Cela veut dire que le robot dévie à gauche par
  // rapport à la ligne qu’il doit suivre. On corrige en tournant à droite
  // jusqu’à ce que la ligne soit à nouveau entre les deux capteurs.
  if((valeur_gauche < seuil_gauche) && (valeur_droite > seuil_droite)) {
    moteur_droite();

    // Attend que le capteur de droite identifie le sol.
    while(analogRead(CAPTEUR_DROITE) > seuil_droite){
      if(digitalRead(ETALONNAGE_BOUTON) == 1){ 
        etalonnage(); 
        break;
      }
      delay(1);
    } 

    return;
  }

  // Tourne à gauche si le capteur de gauche identifie la ligne et le capteur de
  // droite identifie le sol. Cela veut dire que le robot dévie à droite par
  // rapport à la ligne qu’il doit suivre. On corrige en tournant à gauche
  // jusqu’à ce que la ligne soit à nouveau entre les deux capteurs.
  if((valeur_gauche > seuil_gauche) && (valeur_droite < seuil_droite)) {
    moteur_gauche();

    // Attend que le capteur de gauche identifie le sol.
    while(analogRead(CAPTEUR_GAUCHE) > seuil_gauche){
      if(digitalRead(ETALONNAGE_BOUTON) == 1){ 
        etalonnage(); 
        break;
      }
      delay(1);
    }
    return;
  }

  // Arrête le robot si les deux capteurs identifient chacun le sol. Cela veut
  // dire que le robot a perdu la ligne, il est plus prudent de l’arrêter.
  if((valeur_gauche > seuil_gauche) && (valeur_droite > seuil_droite)) { 
    moteur_arret();
    return;
  }
}

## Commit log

2018-09-16 with NPN transistors
    [robot-plus simple.fzz]
2018-10-30 some fixes
    [chassis.dxf, chassis.scad, chassis.stl]
2019-02-11 [PATCH 1/2] Code cleaning Added schematics
2019-02-11 [PATCH 2/2] Simplified circuit version included More comments in the program
2019-02-18 ecartement pour le trou dans la plaque
2019-02-24 remove useless files
    [roue.g, roue2.g]
